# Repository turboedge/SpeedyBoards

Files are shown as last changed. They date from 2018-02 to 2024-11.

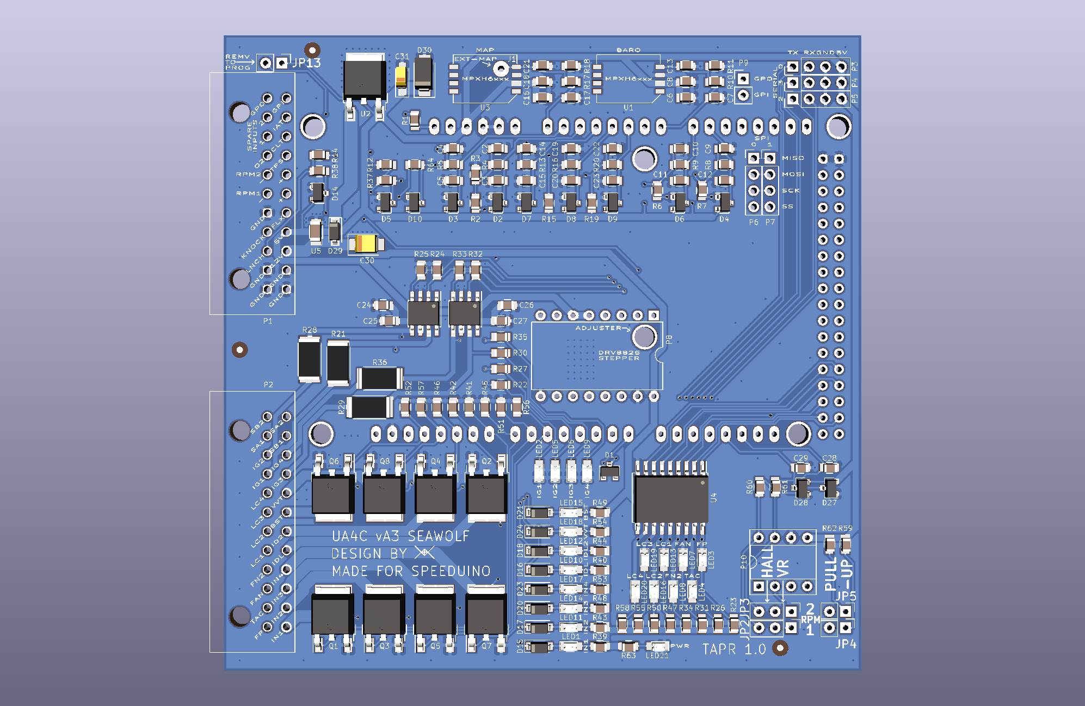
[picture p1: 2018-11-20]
UA4C/vA3-SEAWOLF/RENDER/UA4C-FRONT.png

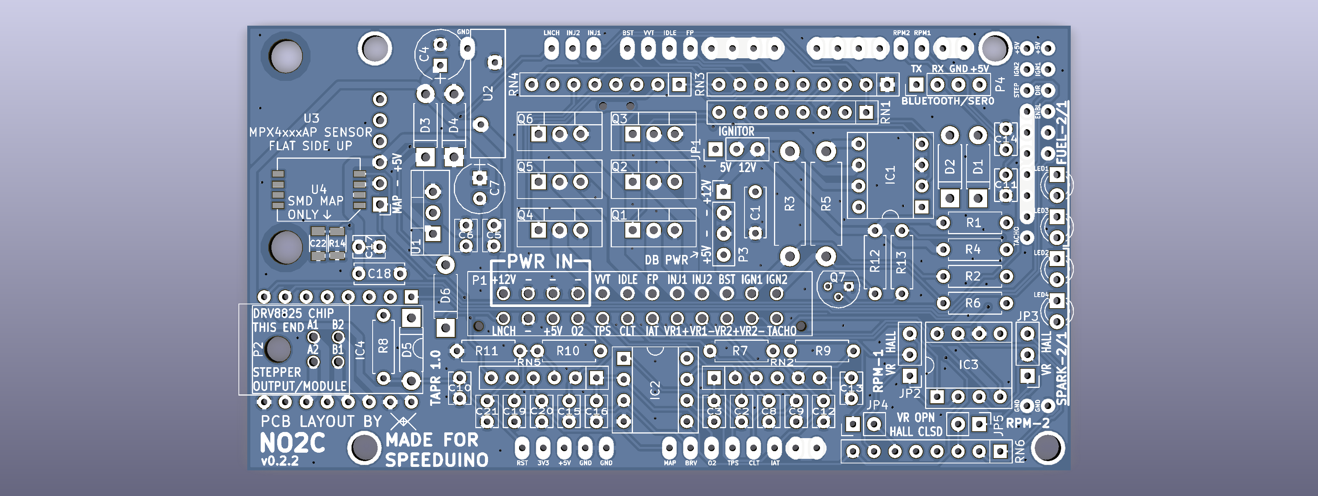
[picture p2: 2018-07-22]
NO2C/v0.2.x/v0.2.2/RENDER/NO2C-FRONT.png

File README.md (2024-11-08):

# SpeedyBoards
WTMtronics has developed several EMS PCBs designed to use the Speeduino firmware.
The Speeduino code is available here [Speeduino](https://github.com/noisymime/speeduino), but the easiest way to load the code onto your ECU is to use [SpeedyLoader](https://github.com/speeduino/SpeedyLoader).
## Ocelot
The latest ECU designed by WTMtronics builds on the UA4C that came before it, and in fact if you compare the two side by side you will see many similarities. However there have been many improvements over the previous model which are outlined in the list below.
- Automotive connector
- Reduced size
- Integrated microcontroller
- VSS input
- Flyback diodes
- Reset button

The reset button was added as the only reset connection made to the microcontroller to prevent unwanted resets from USB connected devices. There is a caveat to this arrangement though. While the first time a firmware is loaded it will go on without intervention, subsequent times will require the user to hold the reset button down then release the button when the program starts the upload process. If the upload does not start right away go back and try again.

The Ocelot uses the Silicon Labs CP2102N USB to UART controller chip. Most modern computers will detect and automatically load a driver for the COM port. If you are not getting the COM port, then you can download drivers from their website [Silicon Labs Drivers](https://www.silabs.com/developers/usb-to-uart-bridge-vcp-drivers).

Latest version: A3 *First release
### Errata
vA3:
- Labeling for trigger jumpers is reversed. The secondary trigger jumpers are nearest the outside edge of the board, and the primary trigger jumpers are near the trigger conditioner socket.
- Serial numbers prior to 002287 will not operate with out a USB connection if no Bluetooth adapter is attached. If your serial number is 002287 or higher this issue does not affect your unit. If you are affected by this issue, please contact us so we can help you [WTMtronics Help](https://wtmtronics.com/help).
## UA4C
The Under Arduino Four Channel was designed to be as small as possible wile still using a standard off the shelf Arduino MEGA and Hammond extruded enclosure. This was achieved by using SMD components and placing the Arduino upside-down on top of the PCB. The unique stacking arrangement allows the unit to be particularly thin for a unit that still uses a separate Arduino MEGA. It is a 4+4 board that incorporates the follow features.
- Four injector channels
- Four ignitor channels
- Outputs for VVT, 2x PWM idle, boost, fuel pump, tachometer, and 2x fan
- Four auxiliary outputs
- Built in stepper idle control (versions C)
- Two trigger inputs
- Launch input
- Two additional interrupt input designated as flex and knock*
- Analog inputs for CLT, IAT, TPS, and O2
- Two auxiliary analog inputs
- MAP and baro sensor onboard
- Two GPIO connections that breakout inside the case

Latest version: C6

*Knock is currently unsupported in the firmware. Either input can be used for VSS.
## NO2C
The No Overhang Two Channel was designed to incorporate as many features as possible into a through-hole board that does not exceed the dimensions of the Arduino MEGA microcontroller it sits on top of. It is a 2+2 channel board that incorporates the features below.
- Two injector channels
- Two ignitor channels
- Outputs for VVT PWM idle, boost, fuel pump, and tachometer
- Two trigger inputs
- Launch input
- Analog inputs for CLT, IAT, TPS, and O2
- MAP sensor onboard
- Socket for stepper idle control module

Latest version: D1

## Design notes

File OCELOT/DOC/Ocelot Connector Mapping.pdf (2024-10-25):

All outputs (except ignitor and stepper idle) are ground switching. Connect at least two ground terminals to a single ground source.
Connector Terminal | Arduino Pin | Function
1 | | GPI | 25 | | STEPPER IDLE A1
2 | | GPO | 26 | D34 | IGNITOR 4
3 | A8 | SPARE INPUT 1 | 27 | D33 | IGNITOR 3
4 | A9 | SPARE INPUT 2 | 28 | D28 | LOW CURRENT OUTPUT 3
5 | | 5V OUT | 29 | D27 | LOW CURRENT OUTPUT 2
6 | | KEYED 12V INPUT | 30 | D25 | FAN 2
7 | | GROUND | 31 | D22 | TACHOMETER
8 | | STEPPER IDLE A2 | 32 | D6 | INJECTOR 3
9 | | STEPPER IDLE B1 | 33 | A5 | INLET AIR TEMPERATURE SENSOR
10 | | UNSWITCHED 12V INPUT (FLYBACK FOR IDLE, BOOST, VVT) | 34 | D37 | LAUNCH/CLUTCH
11 | D29 | LOW CURRENT OUTPUT 4 | 35 | D2 | VEHICLE SPEED SENSOR
12 | D11 | VVT | 36 | D21 | KNOCK SENSOR
13 | D12 | BOOST | 37 | D18 | SECONDARY TRIGGER
14 | D10 | PWM IDLE 2 | 38 | D19 | PRIMARY TRIGGER
15 | D9 | PWM IDLE 1 | 39 | | GROUND
16 | D5 | INJECTOR 4 | 40 | | GROUND
17 | A1 | EXHAUST GAS SENSOR | 41 | | STEPPER IDLE B2
18 | A3 | THROTTLE POSITION SENSOR | 42 | D36 | IGNITOR 2
19 | A4 | COOLANT TEMPERATURE SENSOR | 43 | D35 | IGNITOR 1
20 | D20 | FLEX FUEL SENSOR | 44 | D26 | LOW CURRENT OUTPUT 1
21 | | SECONDARY TRIGGER (VR- ONLY) | 45 | D24 | FAN 1
22 | | PRIMARY TRIGGER (VR- ONLY) | 46 | D23 | FUEL PUMP
23 | | GROUND | 47 | D7 | INJECTOR 2
24 | | GROUND | 48 | D8 | INJECTOR 1
1 | 2 | 3 | 4 | 5 | 6 | 7 | 8 | 9 | 10 | 11 | 12 | 13 | 14 | 15 | 16
17 | 18 | 19 | 20 | 21 | 22 | 23 | 24 | 25 | 26 | 27 | 28 | 29 | 30 | 31 | 32
33 | 34 | 35 | 36 | 37 | 38 | 39 | 40 | 41 | 42 | 43 | 44 | 45 | 46 | 47 | 48

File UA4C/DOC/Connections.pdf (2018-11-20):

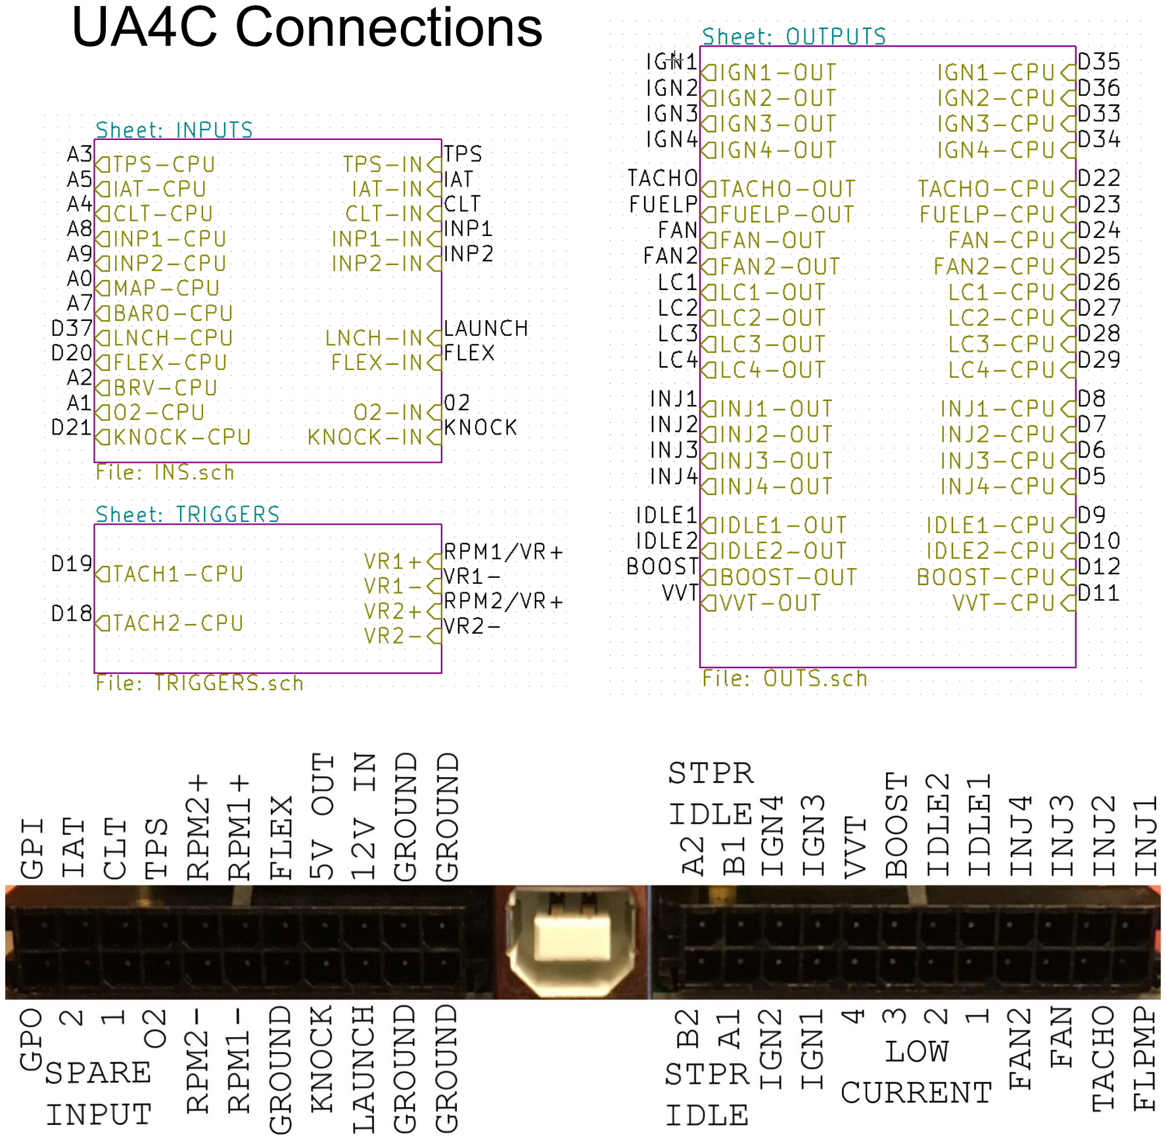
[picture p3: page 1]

UA4C Connections

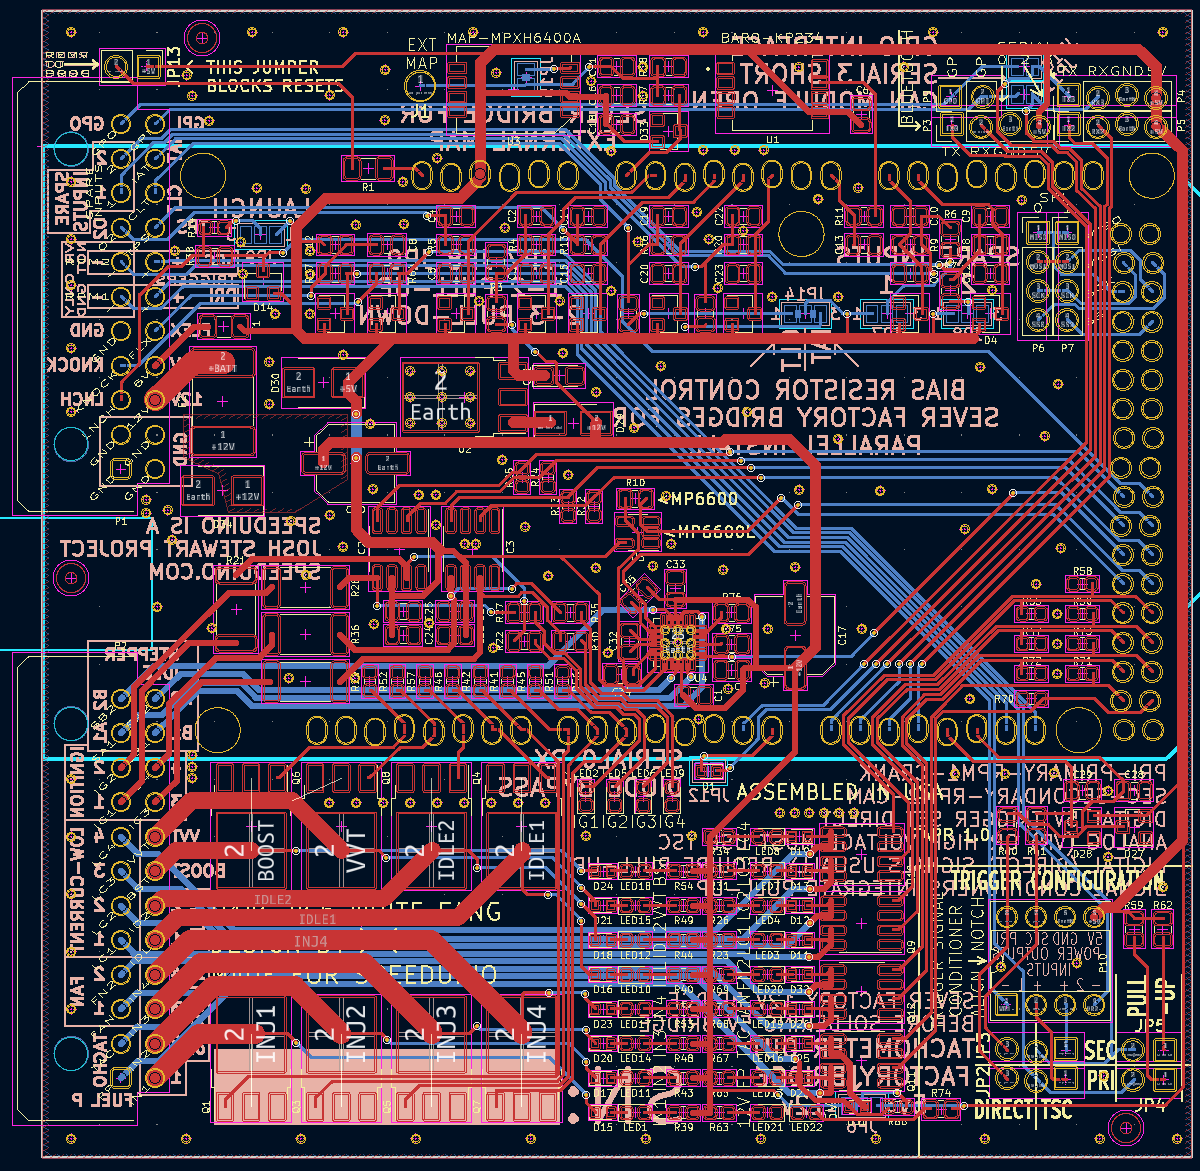
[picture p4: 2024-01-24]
UA4C/vC5-WHITE FANG/RENDER/PCB.PNG

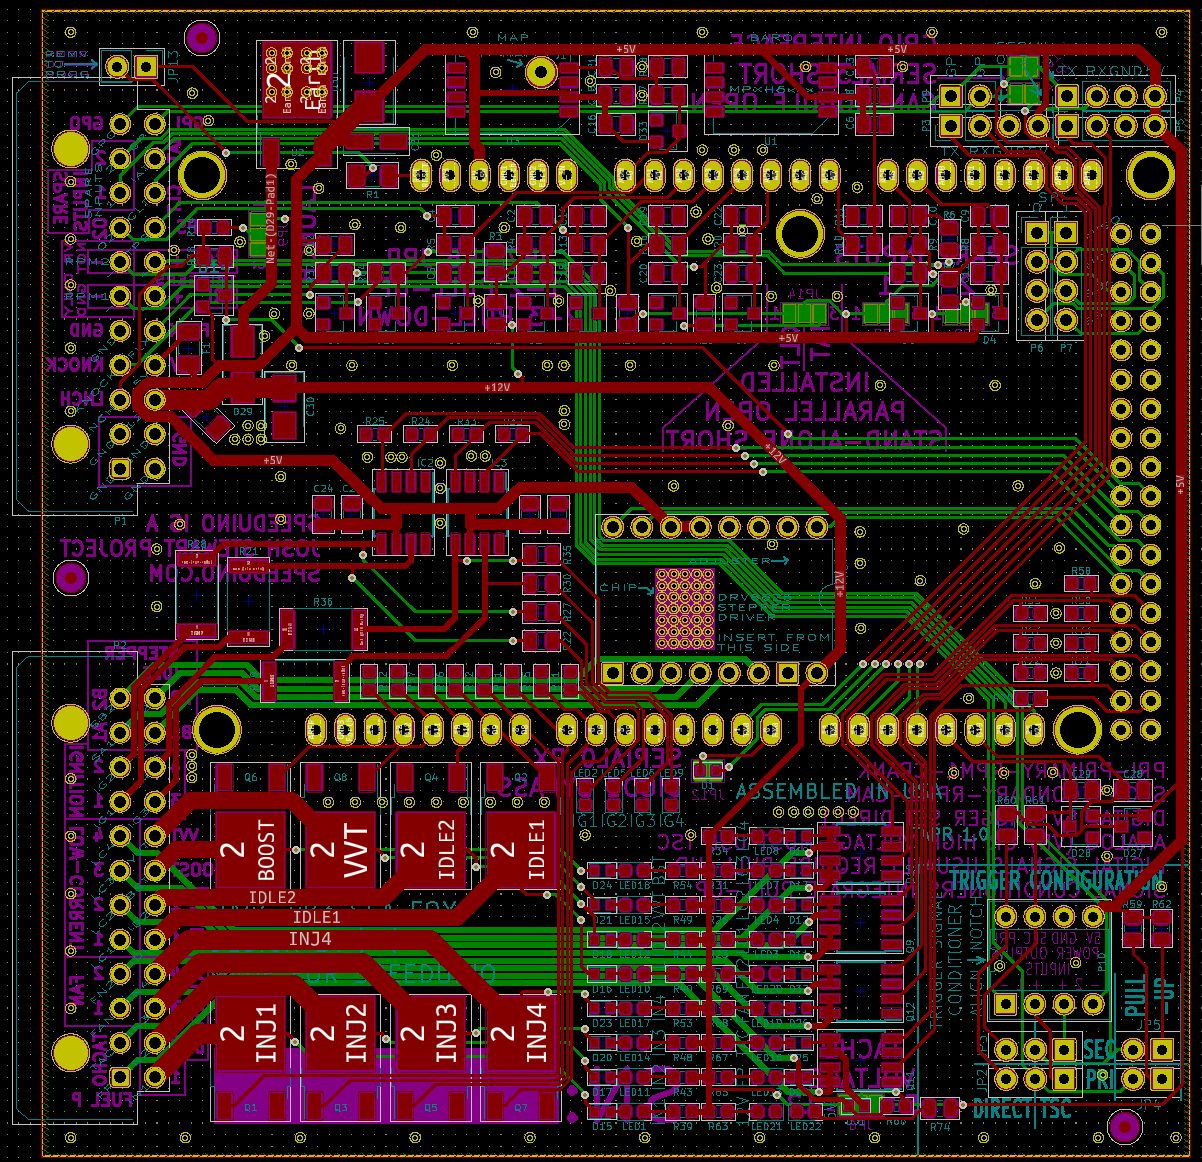
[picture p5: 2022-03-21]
UA4C/vB3-SEA FOX/RENDER/PCB.PNG

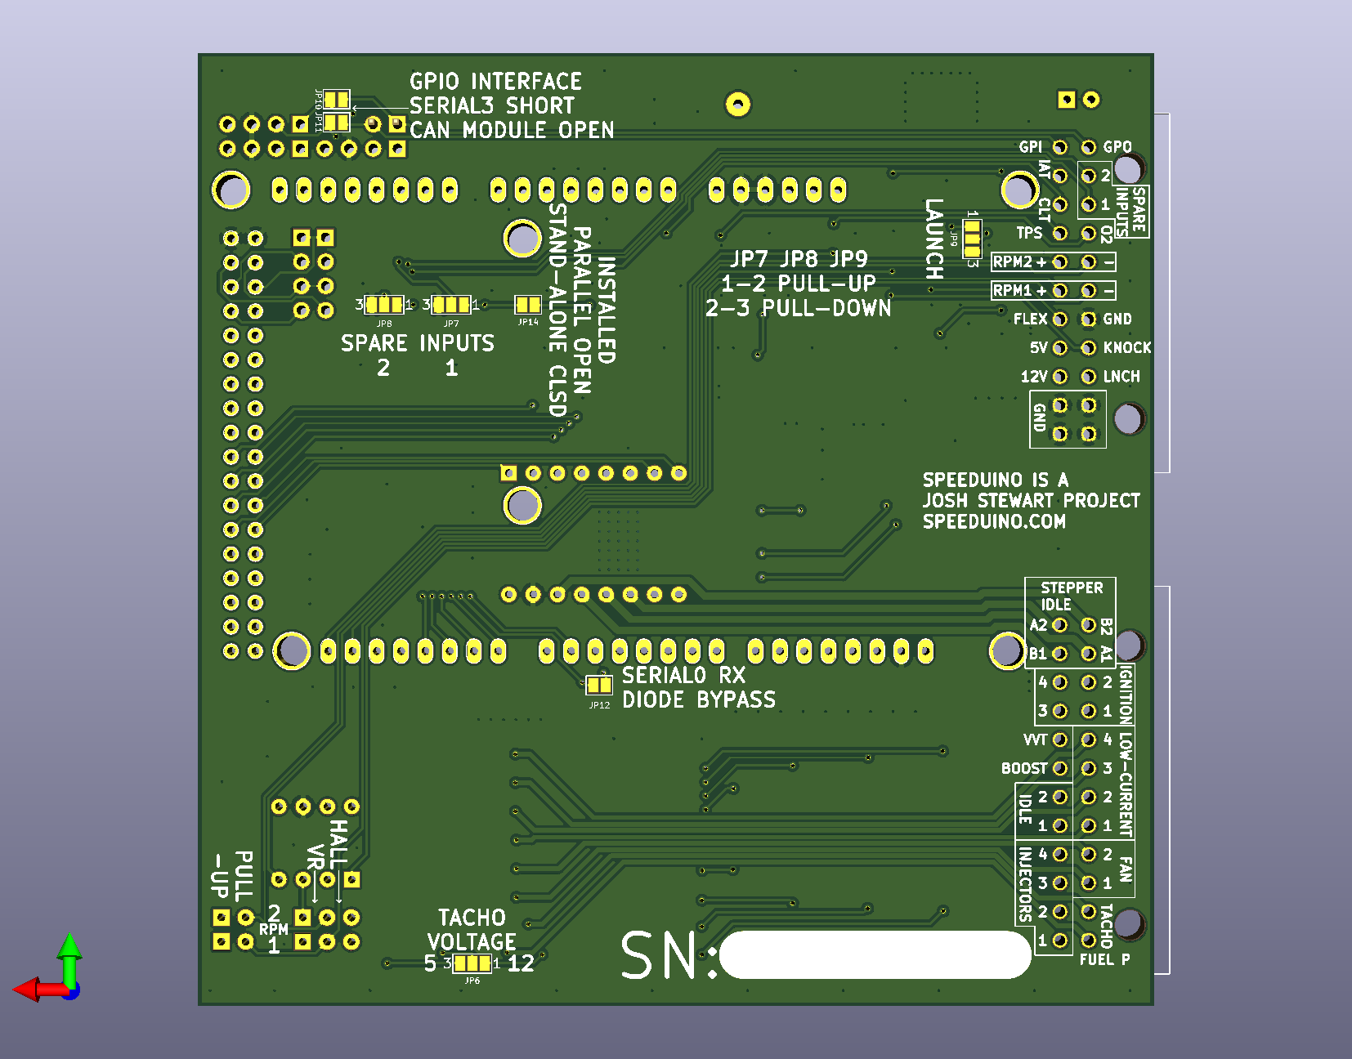
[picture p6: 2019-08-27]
UA4C/vB1-SEA FOX/RENDER/BACK.png

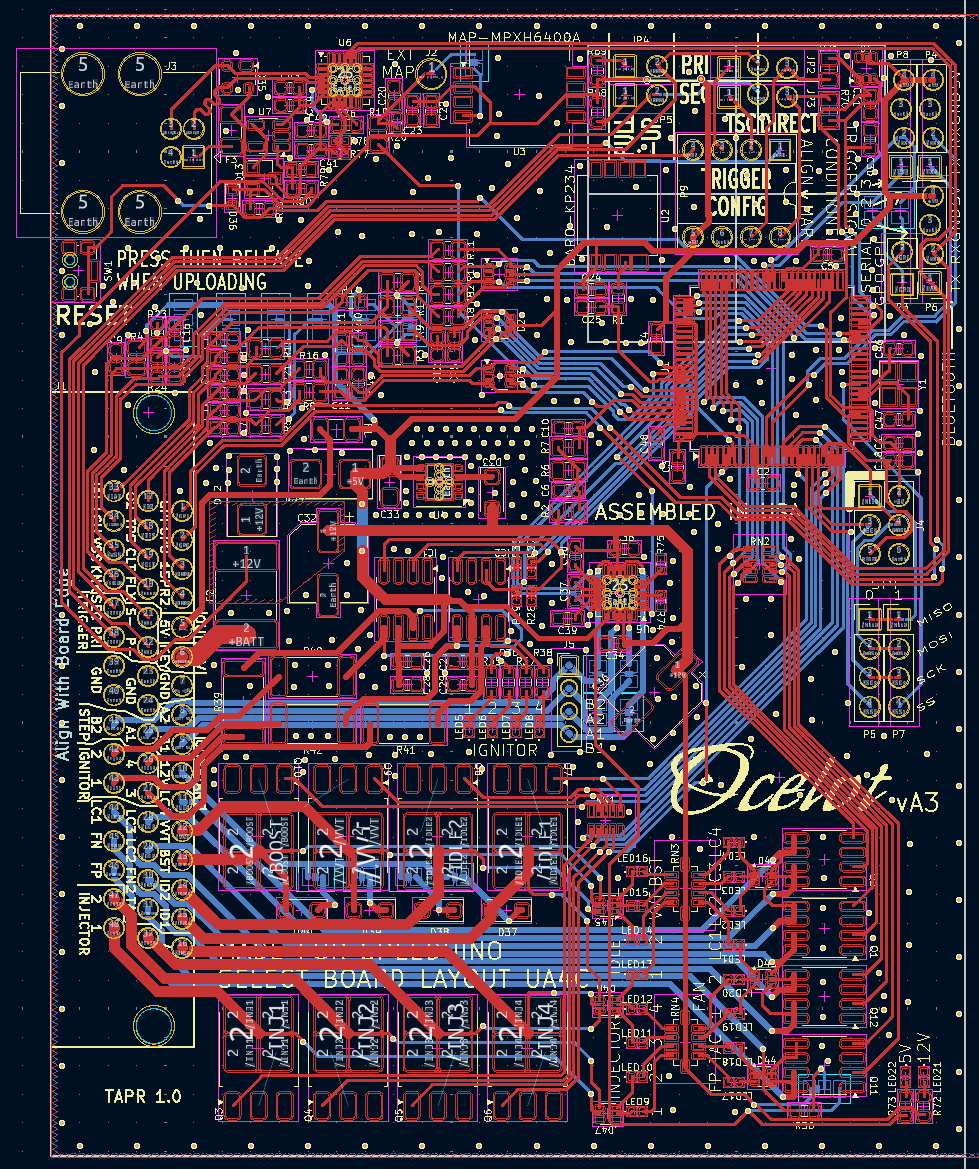
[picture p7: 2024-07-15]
OCELOT/RENDER/CAD.png

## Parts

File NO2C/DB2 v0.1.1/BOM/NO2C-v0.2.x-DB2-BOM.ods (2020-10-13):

Designator | Package | Quantity | Designation | MPN1 | MPN2 | MPN3
R13,R14 | R_1206 | 2 | 1k | RC1206JR-071KL
R1 | R_1206 | 1 | 51k | RK73H2BTTD5102F
R9,R10 | R_Axial_DIN0207_L6.3mm_D2.5mm_P7.62mm_Horizontal | 2 | 2k | MFR-25FBF52-2K
R8,R7 | R_Axial_DIN0411_L9.9mm_D3.6mm_P12.70mm_Horizontal | 2 | 47 2w | FMP200JR-52-47R
R3,R4 | R_Axial_DIN0207_L6.3mm_D2.5mm_P7.62mm_Horizontal | 2 | 1k | MFR-25FBF52-1K
R11 | R_Axial_DIN0207_L6.3mm_D2.5mm_P7.62mm_Horizontal | 1 | 470r | MFR-25FBF52-470R
R6,R5 | R_Axial_DIN0207_L6.3mm_D2.5mm_P7.62mm_Horizontal | 2 | 100k | MFR-25FBF52-100K
R12,R2 | R_Axial_DIN0207_L6.3mm_D2.5mm_P7.62mm_Horizontal | 2 | 2k49 0.1% | YR1B2K49CC
RN1 | R_Array_SIP6 | 1 | 470r | 4606X-102-471LF | L063S471LF
D4,D6,D5,D3 | SOT-23 | 4 | BAT54S | BAT54SRF
D1,D2 | LED_D3.0mm | 2 | T1 RED | SLX-LX3044HD | LTL-4221N
C3 | C_1206 | 1 | 47p | CL31C470JCCNNNC
C5 | C_Disc_D3.8mm_W2.6mm_P2.50mm | 1 | u1 | K104K15X7RF53L2 | RCER71H104K0DBH03A
C1 | C_Disc_D3.8mm_W2.6mm_P2.50mm | 1 | u01 | SR155C103KARTR1 | K103K15X7RF5TL2
C6 | C_Disc_D3.8mm_W2.6mm_P2.50mm | 1 | u22 | FK18X7R1H224K | FG18X7R1H224KRT06 | RHEL81H224K1A2H03B
C4,C2 | C_Disc_D6.0mm_W2.5mm_P5.00mm | 2 | 1u | RDER71H105K2K1H03B
IC2 | DIP-8_W7.62mm | 1 | ICL7667 | IXDN602PI | TC4424AVPA | TC4424EPA
IC1 | SOIC-16_3.9x9.9mm_Pitch1.27mm | 1 | ULN2003A | ULN2003AIDR
U1 | NXP_Pressure_Sensor_SSOP | 1 | DIL8 | MPXHZ6115A6U
P1 | Board Mount 3mm connector-12 position |  |  | 4-794630-2
P2 | Included in 4 position header socket count
P3 | Pigtail for Bluetooth
 | Long tail header pins for NO2C 18 pins required | 1 |  | 929834-03-18 | 929834-03-36 | RK versions ok, p#s are half and full strip
 | 2 position header socket | 3 |  | 75915-302LF
 | 4 position header socket | 2 |  | 75915-304LF
 | 6 position header socket | 1 |  | 75915-306LF
 | Wire Housing 3mm connector-12 position |  |  | 1-794617-2 | From car harness
 | Female pins for above |  |  | 794606-1
 | Panel Mount 3mm housing-12 position |  |  | 1-794615-2 | If you want to route all connections to end of case
 | Male pins for above |  |  | 1-794608-0

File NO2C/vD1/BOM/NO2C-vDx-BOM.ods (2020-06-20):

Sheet: Sheet1
Designator | Package – Description | Quantity | Designation | MPN1 | MPN2 | MPN3 | Alt Value
D3,D5,D6 | D_DO-41_SOD81_P7.62mm_Horizontal – Diode, Schottky | 3 | 1N5818 | 1N5818 | 1N5819
D4 | D_DO-41_SOD81_P7.62mm_Horizontal – Diode, Zener, 5.6v | 1 | 1N5919BG | 1N5919BG | 1N4734A
D2,D1 | D_DO-41_SOD81_P7.62mm_Horizontal – Diode | 2 | 1N4004 | 1N4004
R8 | R_Axial_DIN0207_L6.3mm_D2.5mm_P7.62mm_Horizontal | 1 | 56r | MFR-25FBF52-56R
R12 | R_Axial_DIN0207_L6.3mm_D2.5mm_P7.62mm_Horizontal | 1 | 10k | MFR-25FBF52-10K
R1,R2,R4,R6 | R_Axial_DIN0207_L6.3mm_D2.5mm_P7.62mm_Horizontal | 4 | 2k | MFR-25FBF52-2K
R13,R15 | R_Axial_DIN0207_L6.3mm_D2.5mm_P7.62mm_Horizontal | 2 | 1k | MFR-25FBF52-1K
R3,R5 | R_Axial_DIN0411_L9.9mm_D3.6mm_P12.70mm_Horizontal | 2 | 47r 2w | FMP200FRF52-160R | ERG-2SJ161 | PR02000201600JR500 | (16r 2w for 5v only) RR02J16RTB
R11 | R_Axial_DIN0207_L6.3mm_D2.5mm_P7.62mm_Horizontal | 1 | 1k 0.1% | YR1B1K0CC | MFP-25BRD52-1K
R10 | R_Axial_DIN0207_L6.3mm_D2.5mm_P7.62mm_Horizontal | 1 | 3k9 0.1% | MFP-25BRD52-3K9 | YR1B3K92CC
R9,R7 | R_Axial_DIN0207_L6.3mm_D2.5mm_P7.62mm_Horizontal | 2 | 2k49 0.1% | YR1B2K49CC
RN4,RN1,RN6 | R_Array_SIP8 | 3 | 1k | 4608X-102-102LF | CSC08A031K00GEK
RN5,RN2 | R_Array_SIP6 | 2 | 470r | 4606X-102-471LF | L063S471LF
RN3 | R_Array_SIP9_Bussed | 1 | 100k | 4609X-101-104LF | CSC09A01100KGEK
LED4,LED2,LED3,LED1 | LED_D3.0mm | 4 | T1 <=10mcd | SLX-LX3044HD | LTL-4221N
C11,C17 | Capacitor_Ceramic_Disc_D3.8mm_W2.6mm_P2.50mm | 2 | u01 50v X7R | SR155C103KARTR1 | K103K15X7RF5TL2
C14,C16,C20,C13,C9,C3 | Capacitor_Ceramic_Disc_D3.8mm_W2.6mm_P2.50mm | 6 | u22 50v X7R | FK18X7R1H224K | FG18X7R1H224KRT06 | RHEL81H224K1A2H03B
C18,C1 | Capacitor_Ceramic_Disc_D6.0mm_W2.5mm_P5.00mm | 2 | 1u 50v X7R | RDER71H105K2K1H03B
C21 | Capacitor_Ceramic_Disc_D3.8mm_W2.6mm_P2.50mm | 1 | u33 50v X7R | RCER71H334K1A2H03B | FG18X7R1H334KRT06 | RHEL81H334K1A2H03B
C5,C15,C19,C2,C12,C8,C6 | Capacitor_Ceramic_Disc_D3.8mm_W2.6mm_P2.50mm | 7 | u1 50v X7R | K104K15X7RF53L2 | RCER71H104K0DBH03A
C4 | Capacitor_Radial_Tantalum_D6.0mm_P2.50mm | 1 | 10u 35v | TAP106K035SCS | T350G106K035AT
C7 | Capacitor_Radial_Tantalum_D6.0mm_P2.50mm | 1 | 47u 6.3v | TAP476K006SCS | T350F476K006AT
U1 | TO-220_Vertical – 5V 1A LDO | 1 | LM2940T-5.0 | LM2940T-5.0/NOPB | LM2940T-5.0/LF08 | L4941BV
U2 | Varistor_Disc_D15.5_W4.2_P7.5 | 1 | ERZ | ERZ-V14D220 | B72214S0140K101
IC4 | 8 POSITION 2.54MM FEMALE SOCKET | 2 | DRV8825 | 75915-308LF | 929974-01-08-RK
IC3 | 4 POSITION 2.54MM FEMALE SOCKET | 2 | Dual VR | 75915-304LF | 929974-01-04-RK
IC2 | DIP-8_W7.62mm | 1 | SP721 | SP721APP
IC1 | DIP-8_W7.62mm | 1 | TC4424 | IXDN602PI | TC4424AVPA | TC4424EPA
Q4,Q3,Q6,Q5,Q2,Q1 | TO-220_Vertical | 6 | STP62NS04Z | STP62NS04Z | STP75NS04Z
Q7 | TO-92 | 1 | 2N6517 | 2N6517BU | PN2222
P1 | Molex_Microfit3_Header_02x12_Straight_43045-2428 | 1 |  | 43045-2412 | 5-794630-4
P2 | Molex_Microfit3_Header_02x02_Angled_43045-040x | 1 |  | 43045-0400
P3 | Pin_Header_Straight_1x04_Pitch2.54mm | 1
JP5,JP4 | Pin_Header_Straight_1x02_Pitch2.54mm | 2
JP3,JP2,JP1 | Pin_Header_Straight_1x03_Pitch2.54mm | 3
U3 | MPX4250A | 1 | MPX4250A | MPX4250AP | MPX4400AP (400 kPa version)
 | SHUNT | 5 |  | 2-382811-1 | STC02SYAN
 | 1 POSITION 2.54MM MALE TIN | 60 |  | 68001-400HLF | (8 position) PREC008SAAN-RC
 | DIP-8_W7.62mm_Socket NOT RECOMMENDED FOR IC2 | 1 |  | 110-99-308-41-001000 | AR 08 HZL-TT
From car harness | Wire Housing 3mm connector-24 position |  |  | 2-794617-4
From car harness for stepper | Wire Housing 3mm connector-4 position |  |  | 794617-4
 | Female pins for above |  |  | 794606-1
For routing 24-pins to case end | Panel Mount 3mm housing-24 position |  |  | 2-794615-4
 | Male pins for above |  |  | 1-794608-0

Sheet: Sheet2
1N5818 | 2
1N5919BG | 1
1N4004 | 2
MFS1/4DCT52R1002F | 2
SFR16S0006800JA500 | 4
PR02000201600JR500 | 2
MFP-25BRD52-3K9 | 1
MFS1/4DCT52R2491F | 2
MFS1/4DCT52R1001F | 2
4608X-102-102LF | 3
4606X-102-471LF | 2
4609X-101-104LF | 1
SLX-LX3044HD | 4
SR155C103KARTR1 | 2
FK18X7R1H224K | 6
K472K15X7RF5TL2 | 1
FK14X7R1H105K | 2
RCER71H334K1A2H03B | 1
K104K15X7RF53L2 | 7
TAP106K035SCS | 1
TAP476K006SCS | 1
LM2940T-5.0/NOPB | 1
ERZ-V14D220 | 1
929974-01-08-RK | 2
929974-01-04-RK | 2
SP721APP | 1
IXDN602PI | 1
STP62NS04Z | 6
PN2222 | 1
1-640456-2 | 1
1-640456-6 | 1
640456-4 | 1
MPX4250AP | 1
2-382811-1 | 5
68000-408HLF | 8
3-640620-2 | 3
3-640620-3 | 2
3-640620-4 | 5
110-99-308-41-001000 | 2

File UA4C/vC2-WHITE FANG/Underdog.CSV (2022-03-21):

Reference | Quantity | Value | Footprint | Datasheet | MPN | PN
C1 C2 C4 C6 C9 C10 C14 C16 C19 C22 C25 C27 C29 C32 C33 | 15 | u1 | Capacitor_SMD:C_0805_2012Metric |  | CL21B104KBFNNNE
C3 C5 C11 C12 C15 C20 C23 C34 | 8 | u22 | Capacitor_SMD:C_0805_2012Metric |  | CL21B224KBFNNNE
C7 C8 C18 C24 C26 C35 | 6 | 1u | Capacitor_SMD:C_0805_2012Metric |  | CL21B105KBFNNNE
C13 C21 | 2 | 47p | Capacitor_SMD:C_0805_2012Metric |  | CL21C470JBANNNC
C28 | 1 | u01 | Capacitor_SMD:C_0805_2012Metric |  | CL21B103KBCNNNC
C17 C30 | 2 | 47u 50v | Capacitor_SMD:CP_Elec_6.3x5.4 | https://datasheet.octopart.com/EEE-FT1H470AL-Panasonic-datasheet-147569663.pdf | EEE-FT1H470AL
C31 | 1 | 47u | Capacitor_Tantalum_SMD:CP_EIA-3216-18_Kemet-A |  | T55A476M6R3C0200 | TCJK476M006R0200
D1 D11 D12 D13 D15 D16 D17 D18 D19 D20 D21 D22 D23 D24 D25 D26 D31 D32 | 18 | BAS70KFILM | Diode_SMD:D_SOD-523 |  | BAS70-02V-V-G-08
D29 | 1 | 60V 1A | Diode_SMD:D_SMA | https://www.diodes.com/assets/Datasheets/ds13002.pdf | B160-E3/61T
D30 | 1 | 1SMB5919BT3G | Diode_SMD:D_SMB | https://www.mouser.com/datasheet/2/308/1SMB5913BT3-D-1292981.pdf | 1SMB5919BT3G | 1SMB5919BT3G
D2 D3 D4 D5 D6 D7 D8 D9 D10 D14 D27 D28 D33 | 13 | BAT54S | Package_TO_SOT_SMD:SOT-23 |  | BAT54S,215
F1 | 1 | 500mA/1A 24V | Fuse:Fuse_1206_3216Metric | https://www.mouser.com/datasheet/2/643/ds-CP-0zcj-series-1664160.pdf | 0ZCJ0050AF2E
IC2 IC3 | 2 | IXDN602SIA | Package_SO:SOIC-8_3.9x4.9mm_P1.27mm |  | IXDN602SIA
J1 | 1 | External MAP Conn | Wire_Pads:SolderWirePad_single_1mmDrill | ~ | DNP
JP10 JP11 JP12 | 3 | SolderJumper_2_Open | Jumper:SolderJumper-2_P1.3mm_Open_Pad1.0x1.5mm |  | DNP
JP4 JP5 JP13 | 3 | PULLUP | footprnt:JPR_2POS_SMLHL |  | DNP
JP14 | 1 | SO/PARA | Connector_Automotive:SolderJumper-3_P1.3mm_Bridged123_Pad1.0x1.5mm_NumberLabels |  | DNP
JP15 | 1 | Onboard MAP Enable | Jumper:SolderJumper-2_P1.3mm_Bridged_Pad1.0x1.5mm | ~ | DNP
JP2 JP3 | 2 | HALL_VR | footprnt:JPR_3POS_SMLHL |  | DNP
JP6 | 1 | TACHSEL | Jumper:SolderJumper-3_P1.3mm_Bridged12_Pad1.0x1.5mm_NumberLabels |  | DNP
JP7 JP8 JP9 | 3 | PULLUPDWN | Jumper:SolderJumper-3_P1.3mm_Open_Pad1.0x1.5mm_NumberLabels |  | DNP
LED1 LED2 LED3 LED4 LED5 LED6 LED7 LED8 LED9 LED10 LED11 LED12 LED13 LED14 LED15 LED16 LED17 LED18 LED19 LED20 LED21 LED22 | 22 | RED | LED_SMD:LED_0603_1608Metric |  | SML-310LTT86
P1 | 1 | INPUTS | Connector_Molex:Molex_Micro-Fit_3.0_43045-2200_2x11_P3.00mm_Horizontal |  | DNP
P10 | 1 | Dual VR C | Housings_DIP:DIP-8_W7.62mm_Socket |  | DNP
P2 | 1 | OUTPUTS | Connector_Molex:Molex_Micro-Fit_3.0_43045-2400_2x12_P3.00mm_Horizontal |  | DNP
P3 | 1 | SER0 | Pin_Headers:Pin_Header_Straight_1x04_Pitch2.54mm |  | DNP
P4 | 1 | SER3 | Pin_Headers:Pin_Header_Straight_1x04_Pitch2.54mm |  | DNP
P5 | 1 | SER2 | Pin_Headers:Pin_Header_Straight_1x04_Pitch2.54mm |  | DNP
P6 | 1 | SPI0 | Pin_Headers:Pin_Header_Straight_1x04_Pitch2.54mm |  | DNP
P7 | 1 | SPI1 | Pin_Headers:Pin_Header_Straight_1x04_Pitch2.54mm |  | DNP
P9 | 1 | CAN | Connector_PinHeader_2.54mm:PinHeader_1x02_P2.54mm_Vertical |  | DNP
Q1 Q2 Q3 Q4 Q5 Q6 Q7 Q8 | 8 | NCV8406 | Package_TO_SOT_SMD:TO-252-2 |  | NCV8406BDTRKG
Q9 Q10 Q11 Q12 | 4 | NCV8402AD | Package_SO:SOIC-8_3.9x4.9mm_P1.27mm | www.st.com/resource/en/datasheet/CD00001537.pdf | NCV8402ADDR2G
R1 | 1 | 56r | Resistor_SMD:R_1206_3216Metric |  | RK73H2BTTD56R0F
R14 R23 R26 R31 R34 R39 R40 R43 R44 R48 R49 R53 R54 R63 R65 R66 R67 R68 R69 | 19 | 2k7 | Resistor_SMD:R_0603_1608Metric |  | RK73B1JTTD272J
R6 R7 R12 R15 R19 | 5 | 2k49 0.1% | Resistor_SMD:R_0805_2012Metric |  | ERA6AEB2491V
R11 R18 R75 | 3 | 51k | Resistor_SMD:R_0805_2012Metric |  | RK73H2ATTD5102F
R2 | 1 | 3k9 0.1% | Resistor_SMD:R_0805_2012Metric |  | ERA6AEB392V
R4 R5 R8 R9 R10 R13 R16 R17 R20 R22 R27 R30 R35 R37 R38 R64 R74 | 17 | 470r | Resistor_SMD:R_0805_2012Metric |  | RK73H2ATTD4700F
R24 R25 R32 R33 R41 R42 R45 R46 R47 R50 R51 R52 R55 R56 R57 R58 R70 R71 R72 R73 | 20 | 100k | Resistor_SMD:R_0603_1608Metric |  | RK73B1JTTD104J
R3 | 1 | 1k 0.1% | Resistor_SMD:R_0805_2012Metric |  | ERA6AEB102V
R21 R28 R29 R36 | 4 | 15r | Resistor_SMD:R_2512_6332Metric |  | RK73H3ATTE15R0F
R60 R61 | 2 | 220r | Resistor_SMD:R_0805_2012Metric |  | RK73H2ATTD2200F
R59 R62 | 2 | 1K | Resistor_SMD:R_0805_2012Metric |  | RK73H2ATTD1001F
R76 | 1 | 220k | Resistor_SMD:R_0805_2012Metric |  | RK73H2ATTD2203F
SHIELD1 | 1 | ARDUINO_MEGA_SHIELD | footprnt:ARDUINO_MEGA_SHIELD |  | DNP
U1 | 1 | BARO | Sensors:NXP_Pressure_Sensor_SSOP |  | MPXH6115A6T1
U2 | 1 | TS2940CP50 | Package_TO_SOT_SMD:TO-252-2 |  | TS2940CP50 ROG
U3 | 1 | MAP | Sensors:NXP_Pressure_Sensor_SSOP |  | MPXH6400AC6U
U4 | 1 | MP6600 | Package_DFN_QFN:QFN-24-1EP_4x4mm_P0.5mm_EP2.7x2.7mm_ThermalVias | https://www.monolithicpower.com/en/documentview/productdocument/index/version/2/document_type/Datasheet/lang/en/sku/MP6600/ | MP6600GR-Z
U5 | 1 | 14v | Capacitor_SMD:C_1206_3216Metric |  | ZV14K1206201NIR1HT

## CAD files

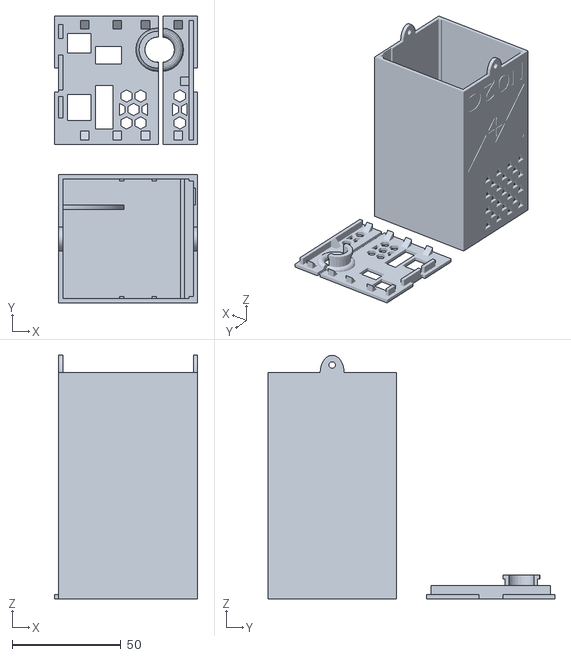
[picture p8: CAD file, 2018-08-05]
Set-NOboxT.stl
66.0 x 132.0 x 112.0

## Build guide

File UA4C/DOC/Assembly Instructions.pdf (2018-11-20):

# UA4C Assembly Instructions

## Use the following directions to turn your mostly assembled UA4C into a

fully assembled UA4C.

If you are going install a stepper driver the best time is now. Insert the module through top of the board with the adjustment pot over the hole in the hole in the UA4C. Flip the UA4C over and solder the pins down and clip the remaining off.

The next step is to attach the BARO and MAP sensors. Pay attention to the clipped corner of the sensor and align it with the markings on the on the board. vA3 has solder already on the sensor pads. Use this solder to tack one of the sensor legs and then adjust its position if necessary. If you have access to flux this can help get it to stick. Now use the finest solder wire available and solder the rest of the legs and touch up the first one if necessary.

Now attach the Arduino and trigger jumper header pins to the top of the board. You should have three strips of 40 pins. Break one of the sticks into five sections of eight and insert them into the board. Take another strip and break four pins off and then break both the section of four and the section of 36 in half. Insert the two pin pieces in the jumper positions where the VR socket will go and the 18 pin pieces in the double row Arduino connection. You will now be left with one more stick. Break one ten and two six pin sections off. Put the ten and one of the six pin sections into the appropriate Arduino locations. The remaining six pin section gets broken in half and used in the final jumper positions by the VR socket. Now take a ~10cm² piece of something flat but not easily melted (a piece of good cardboard) and set it on top of the board. Avoid the MAP sensor as it protrudes. Now flip the sandwich you have created over, again be careful of the MAP sensor, you may need to let it hang off the edge of a table. Press down a bit to make sure all the pins are fully through the board and solder away.

The next step is to attach the VR module socket. Break off two four pin strips from your remaining header pins. Insert them into the sockets suchasthat they create a square. Insert the sockets into the board and while holding them in flip the board and carefully tack a pin in each row with solder. Set the board down and solder the remaining socket pins. Remove the header pins from the socket.

Final step is the card edge with the harness connectors and reset protection jumper. The header jumper can simply be pressed in to its spot in the corner and soldered down. For the harness connectors snap both of them to the board. Now on each connector solder ONE of the middle pins toward the outside edge. Now while squeezing the connector and the PCB together with your finger in the middle of the connector and over ther outside row heat the solder. The connector will snap tight to the board and become level. Repeat for the other connector and then solder all the contacts.

Congrats! You’re Done!

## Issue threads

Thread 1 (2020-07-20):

Some parts missing in BOM vD1

romP44, 2020-07-20:
Hello,
In BOM vD1, some parts are missing:
- P4
- JP6
- C22
- R14

turboedge, 2022-03-22:
I checked over the BOM, and the parts you are referring to are header pins and jumpers. That said some of the parts are a bit out of date with what I currently ship with the kits I send out. I'll try to get this updated soon. I will not be updating the BOMs for the old versions though.

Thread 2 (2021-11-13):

Board is at VC3, source is at VB2?

ElDominio, 2021-11-13:
I saw that there's aa VC3 for sale, but the source only goes to an old revision. Can the source be updated? It is a very good reference for electronic design.

rickyrockrat, 2022-03-20:
I bought a UA4C but no source, so I have no idea what I really have. I wish I had realized this before I bought it. I would have found something else.

turboedge, 2022-03-21:
The files are now posted, sorry for the delay.

rickyrockrat, 2022-03-23:
Thanks! I just built the speeduino from source using this project:
https://github.com/rickyrockrat/speeduino-build

Are there any files I should know about as far as pin mapping? I will work through the schematic and verify the pins are right, but didn't know if you need to supply a header file.  Thanks for the board, BTW! I hope to have my 1uzfe running here soon.

turboedge, 2022-03-23:
Sorry you lost me. Verify what pins, header file? I hope your project goes smoothly.

Closed 2022-03-21.

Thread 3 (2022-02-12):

UA4C BOM?

digitaltrousers, 2022-02-12:
Hi. I notice there are folders with a BOM inside the folders for NO2C. Sorry if I've missed something, but is there a BOM for UA4C?
Thanks.

turboedge, 2022-03-21:
If you open the project source code in Kicad the items are listed there. Good luck finding all the parts, it's been a nightmare.

Closed 2022-03-21.

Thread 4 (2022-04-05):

Updated Assembly Instructions for UA4C vC3 White Fang

masterofsome906, 2022-04-05:
Weaver, Looking to collaborate on updating the assembly instructions for the current UA4C White Fang board.  I've based my writeup on your original and have geared it towards individuals looking to get into the platform without much/any experience with the earlier versions.

masterofsome906, 2022-04-05:
[UA4C vC3 White Fang Assembly Instructions.pdf](https://github.com/turboedge/SpeedyBoards/files/8413895/UA4C.vC3.White.Fang.Assembly.Instructions.pdf)

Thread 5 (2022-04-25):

BAT54S Diode pinout not as shown in schematics?

Afroboltski, 2022-04-25:
The BAT54S datasheet ([https://assets.nexperia.com/documents/data-sheet/BAT54_SER.pdf](https://assets.nexperia.com/documents/data-sheet/BAT54_SER.pdf)) shows the following pinout:

Pin1: Anode
Pin2: N/C
Pin3: Cathode

However in the schematics, e.g. [https://github.com/turboedge/SpeedyBoards/blob/master/UA4C/vB3-SEA%20FOX/SCHEM/Underdog.pdf](https://github.com/turboedge/SpeedyBoards/blob/master/UA4C/vB3-SEA%20FOX/SCHEM/Underdog.pdf), the diodes (e.g. page 2, diode D7) are shown as doubled up, e.g. as if the pinout was as follows:

Pin1: Anode diode 1
Pin2: Cathode Diode 2
Pin3: Cathode Diode 1/Anode diode 2

Using the pinout from the datasheet, you would only have a diode from GND to INPUT, not from INPUT to +5V as shown.

Or is there a different version of the BAT54S that I'm not seeing?

Afroboltski, 2022-04-25:
Never mind me, I mixed up my BAT54 and BAT54S...

Closed 2022-04-25.

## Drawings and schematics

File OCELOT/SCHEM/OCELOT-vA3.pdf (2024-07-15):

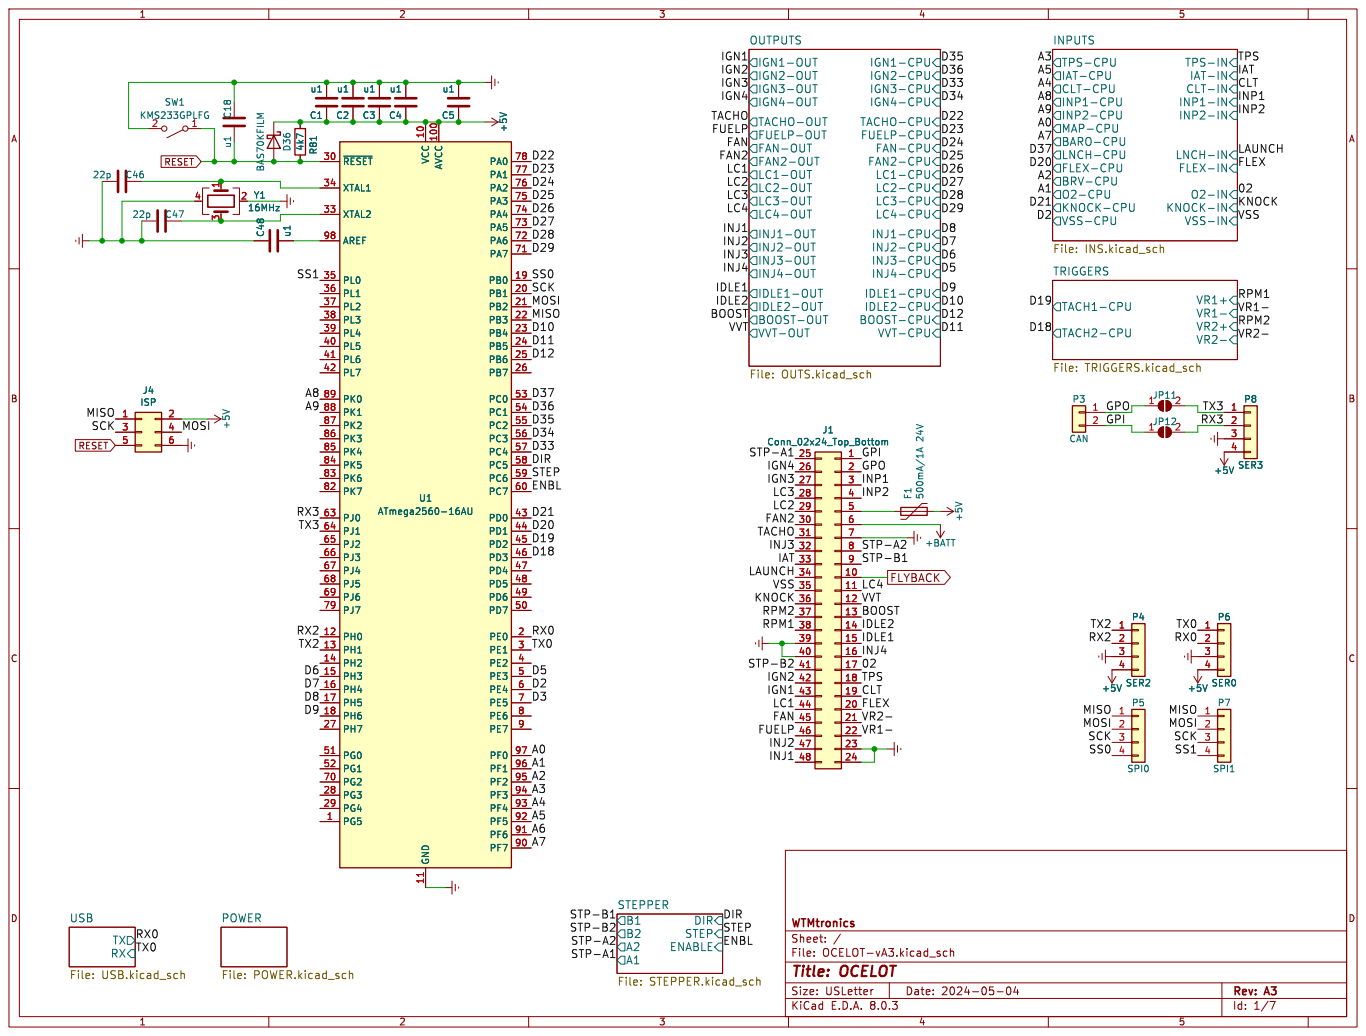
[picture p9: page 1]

File: OCELOT-vA3.kicad_sch Sheet: / WTMtronics TXRX USB

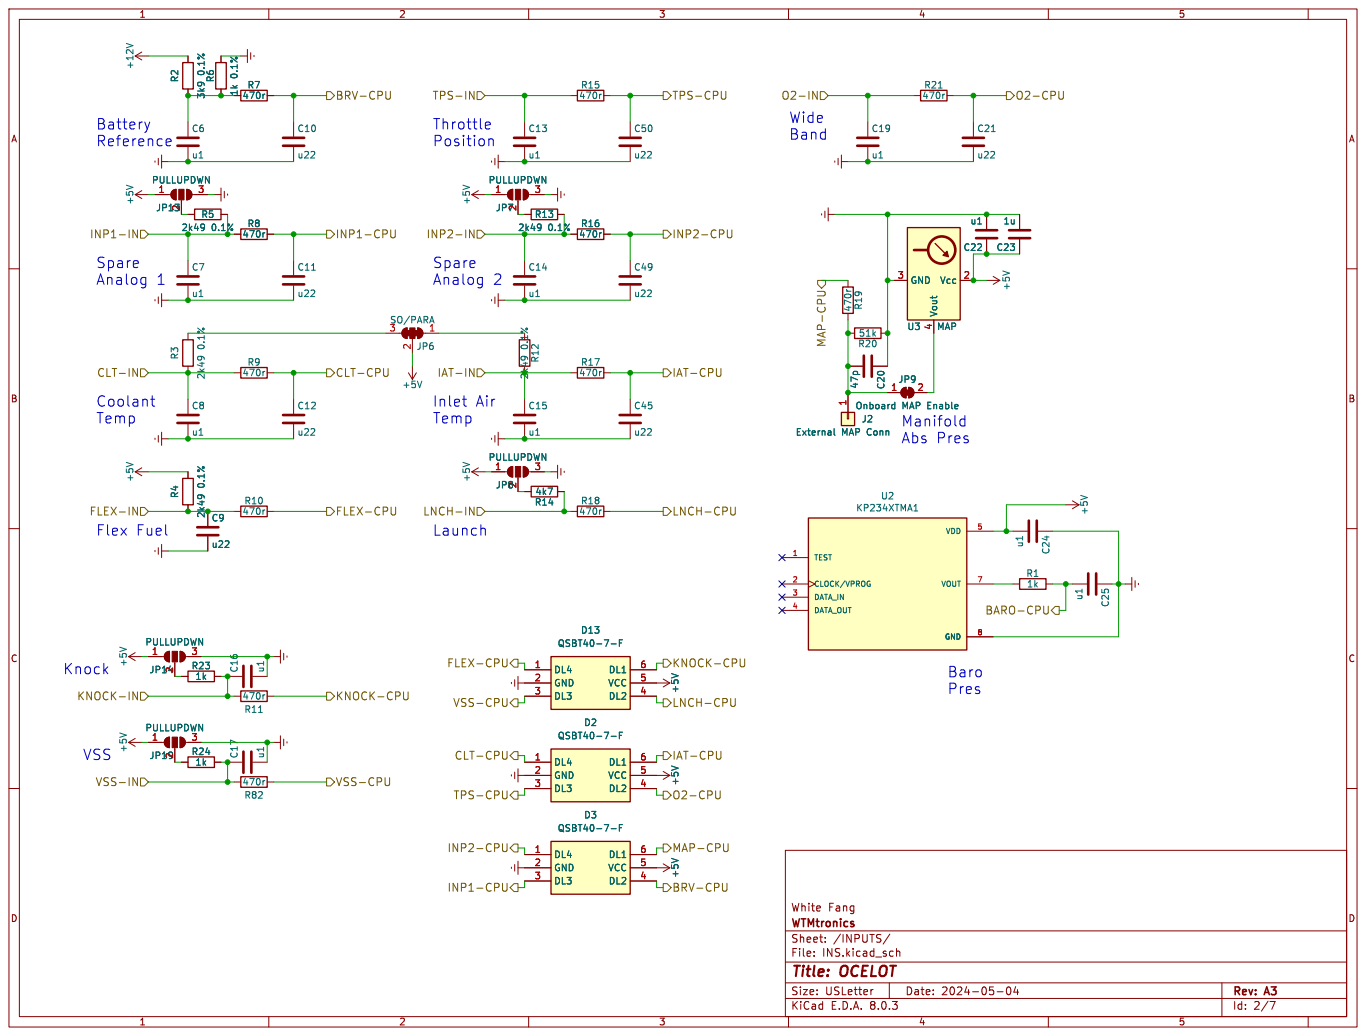
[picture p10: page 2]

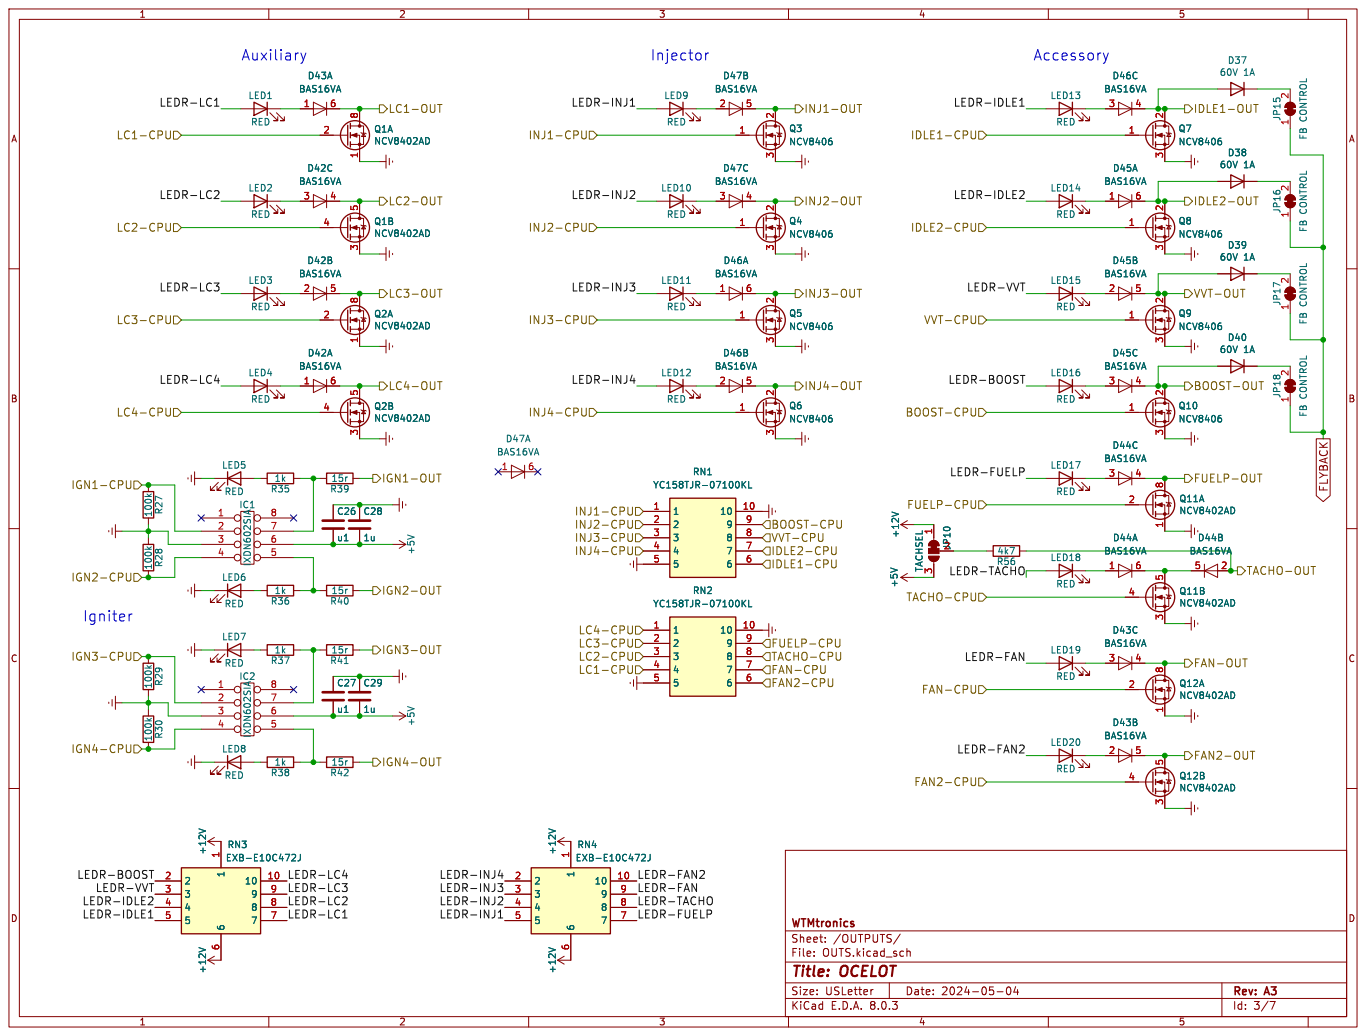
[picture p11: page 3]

File: OUTS.kicad_sch Sheet: /OUTPUTS/ WTMtronics

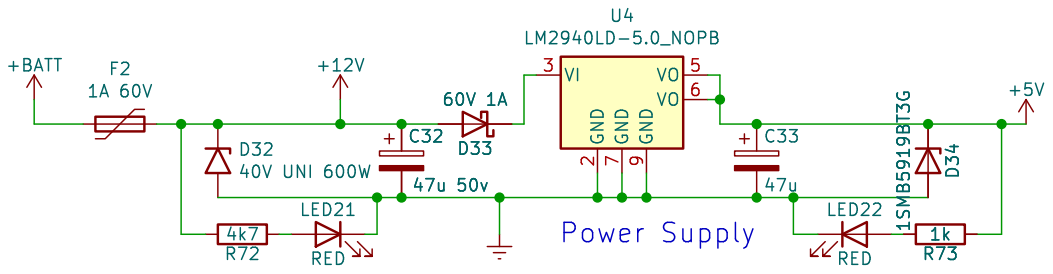
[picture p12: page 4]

2 VI 3 VO 5 VO 6 GND

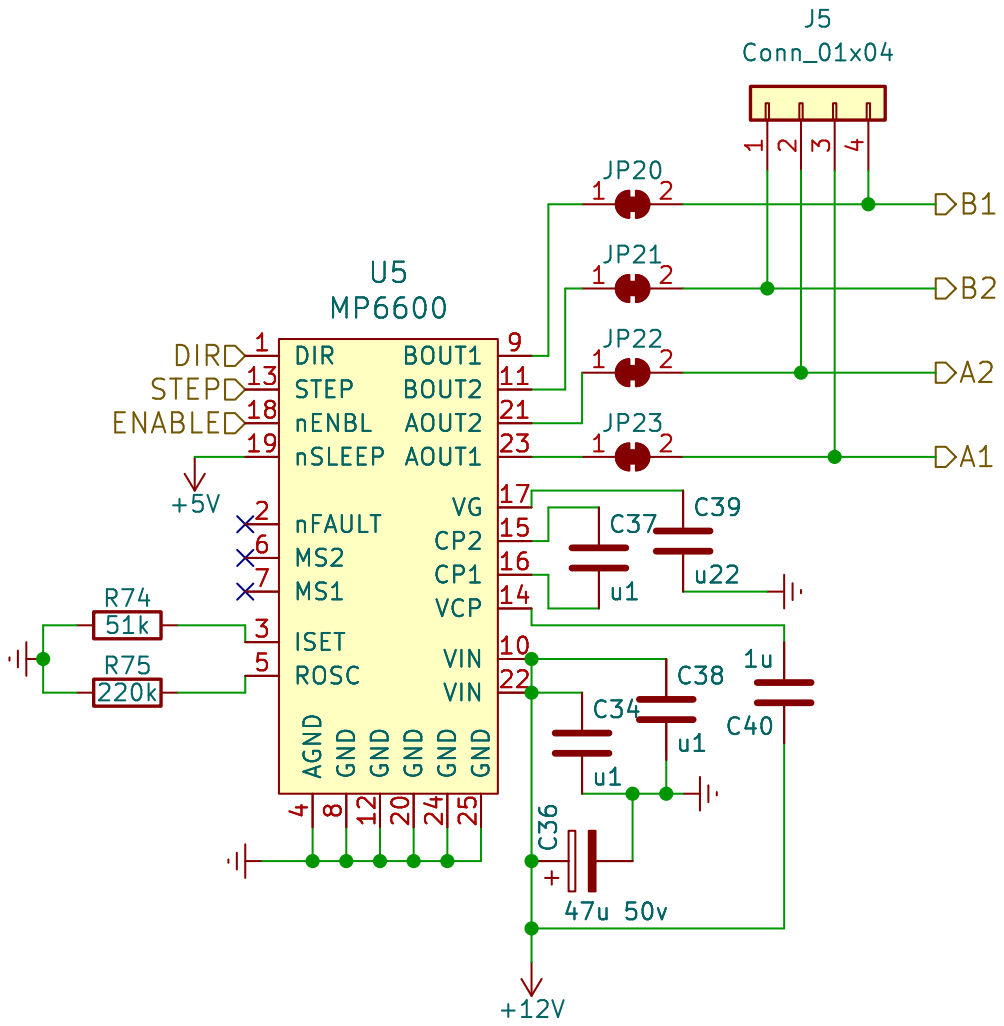
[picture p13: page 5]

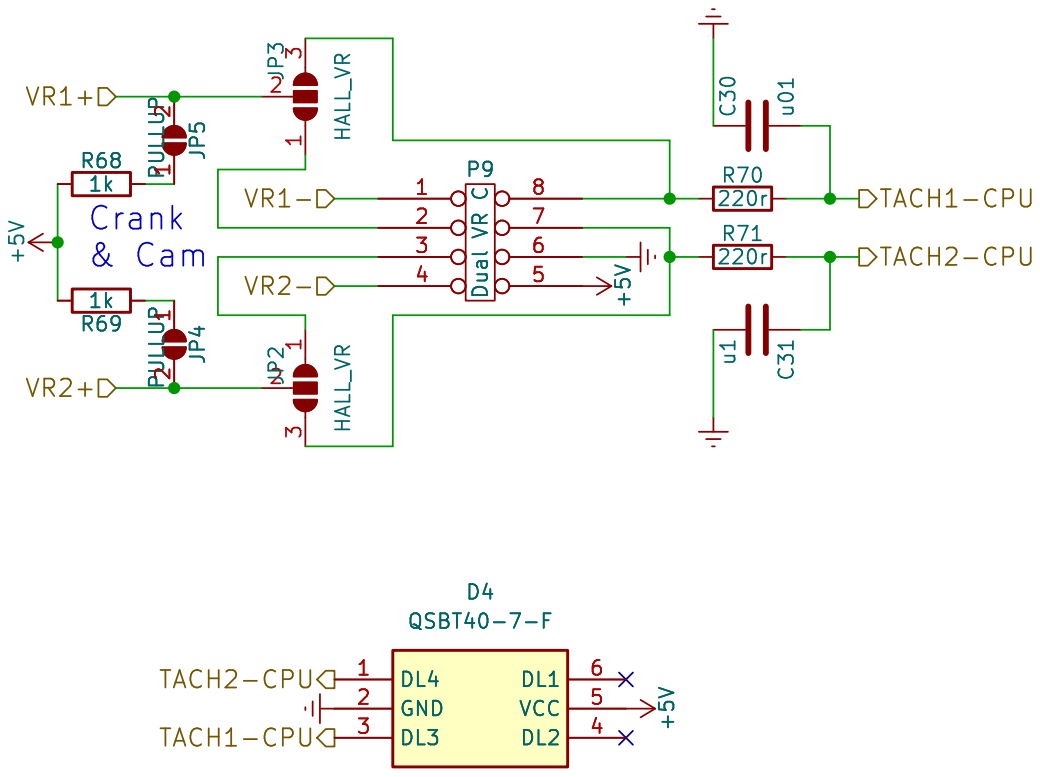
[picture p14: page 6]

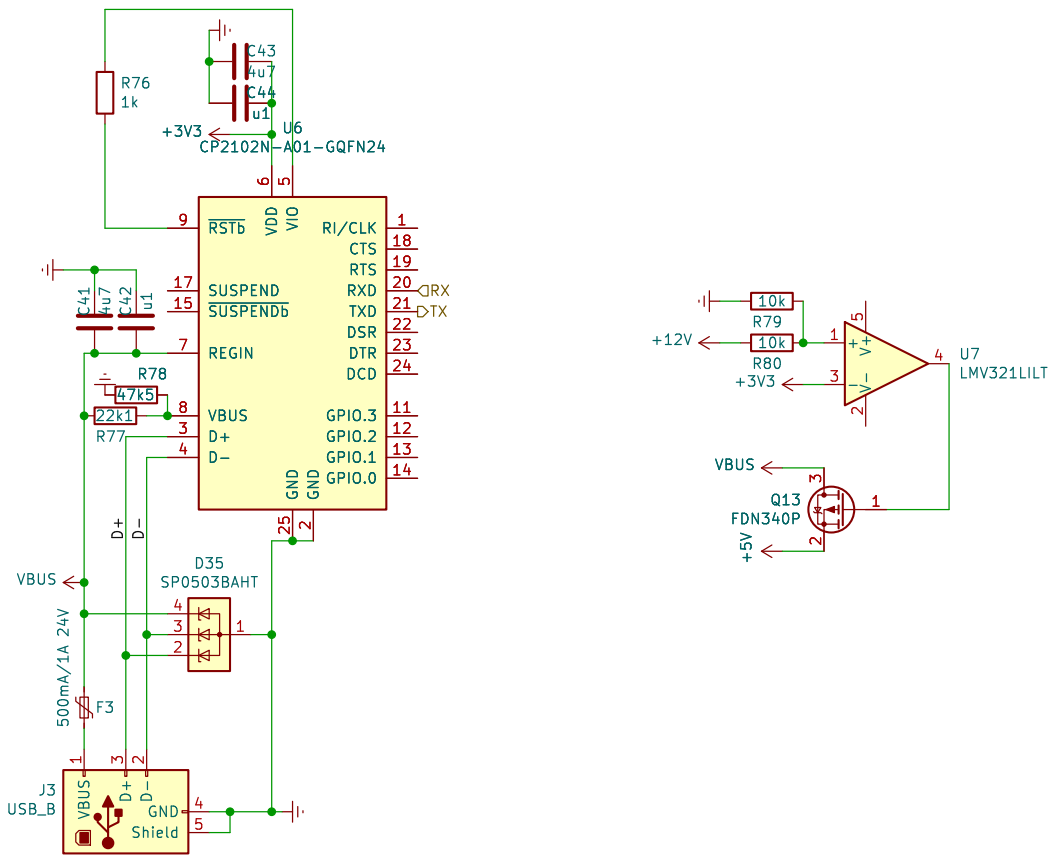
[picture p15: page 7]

File: USB.kicad_sch Sheet: /USB/ WTMtronics

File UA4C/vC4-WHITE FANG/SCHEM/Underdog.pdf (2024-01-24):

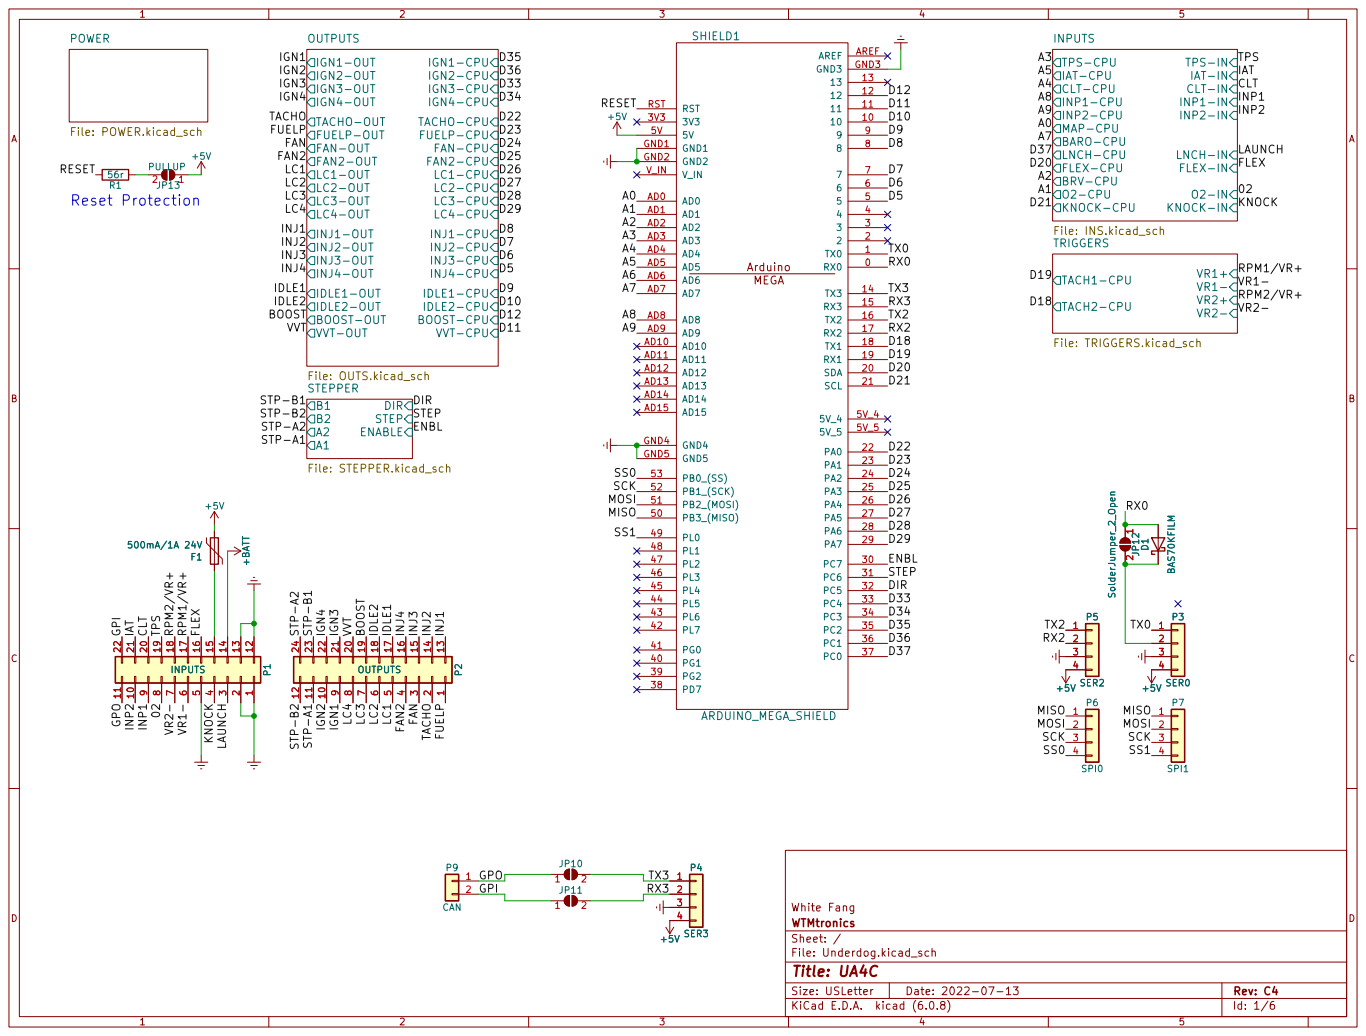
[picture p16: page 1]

File: Underdog.kicad_sch Sheet: / WTMtronics White Fang

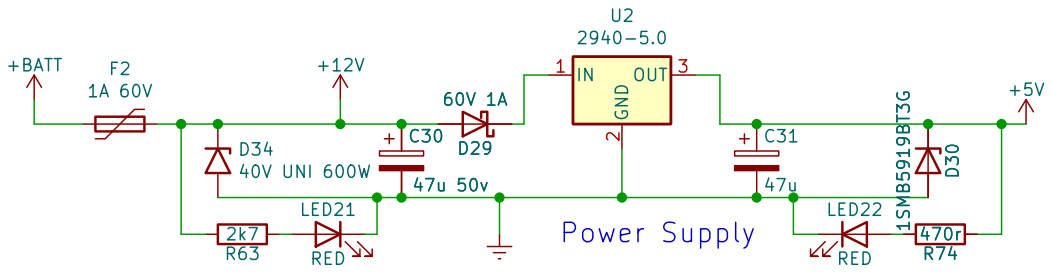
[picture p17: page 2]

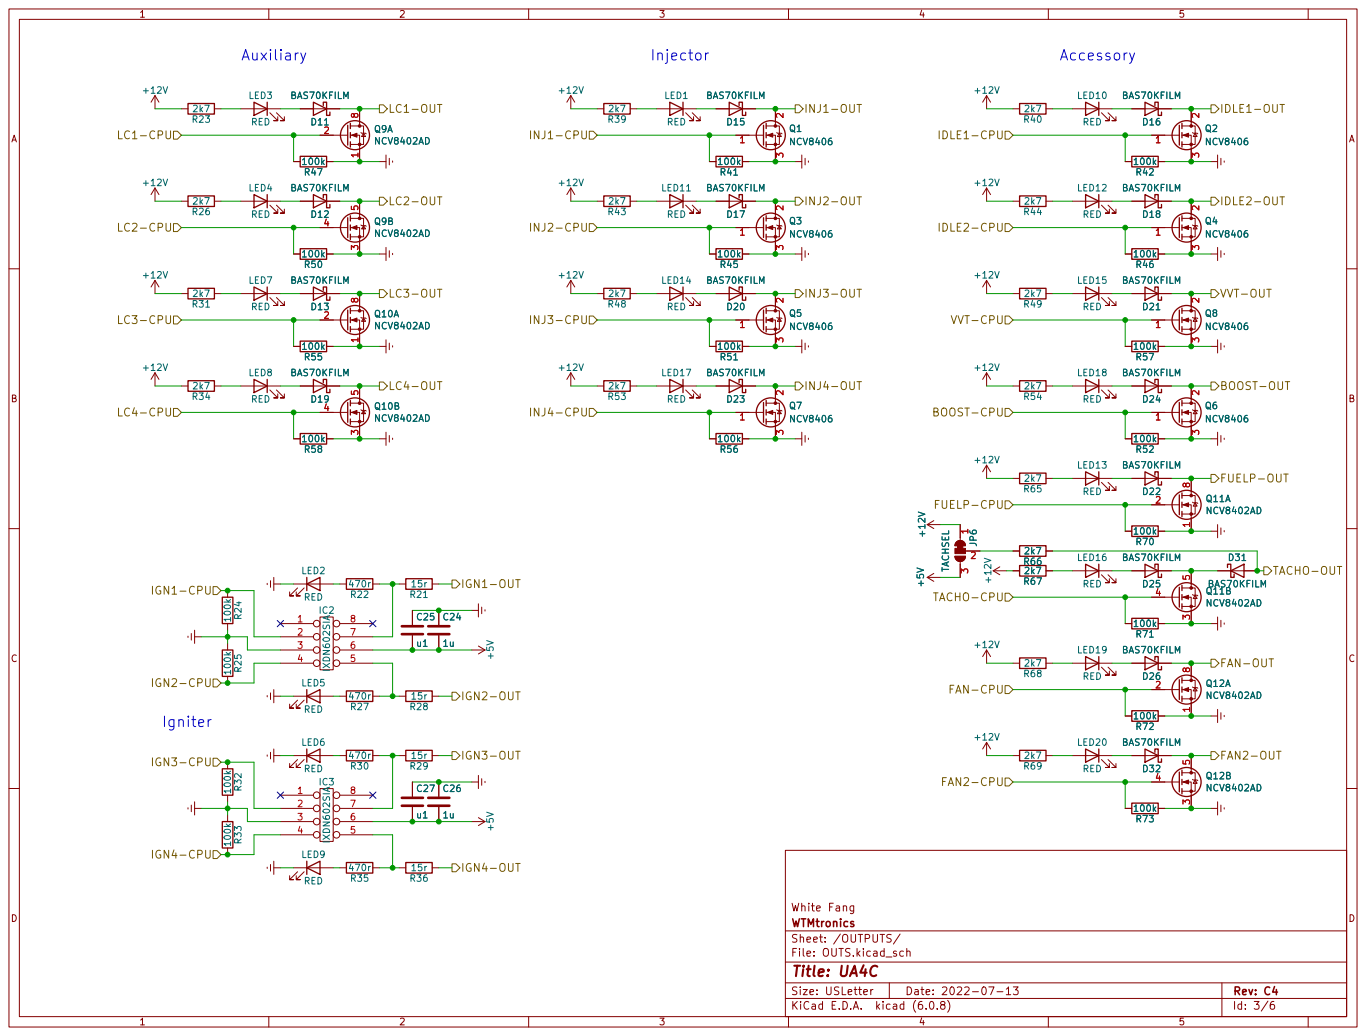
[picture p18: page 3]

File: OUTS.kicad_sch Sheet: /OUTPUTS/ WTMtronics White Fang

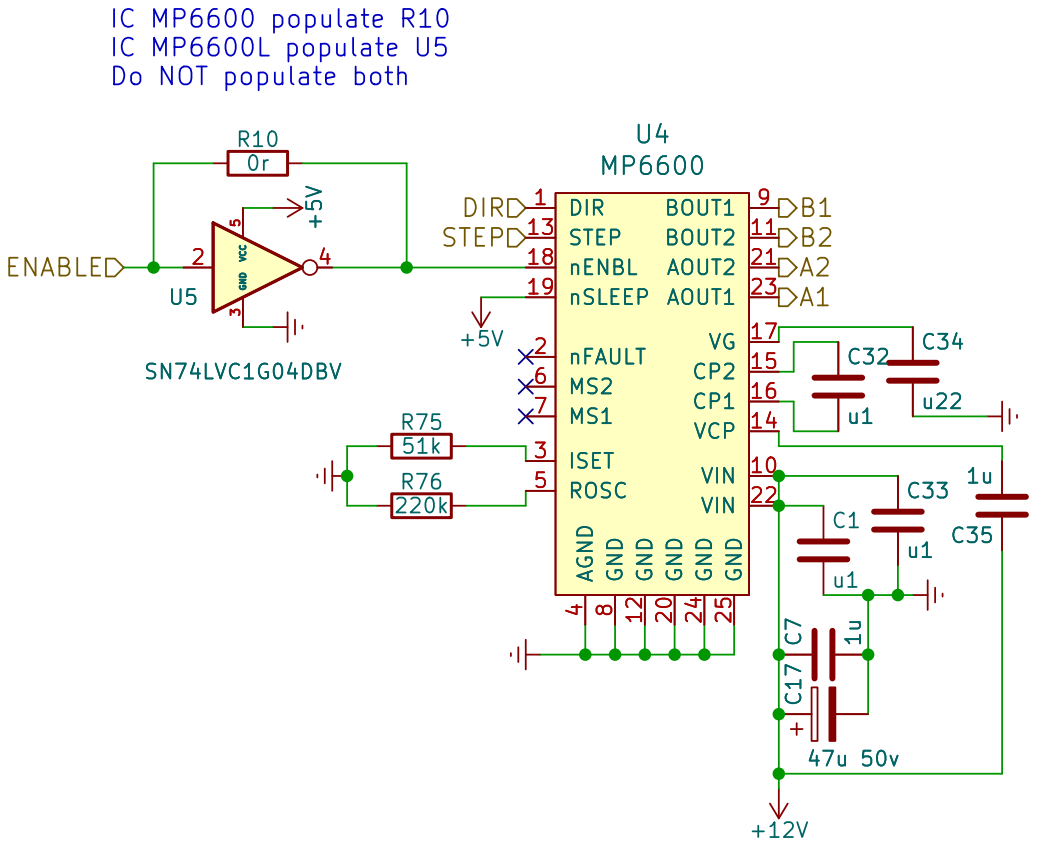
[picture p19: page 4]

IC MP6600 populate R10
IC MP6600L populate U5
File: STEPPER.kicad_sch Sheet: /STEPPER/ WTMtronics White Fang C17

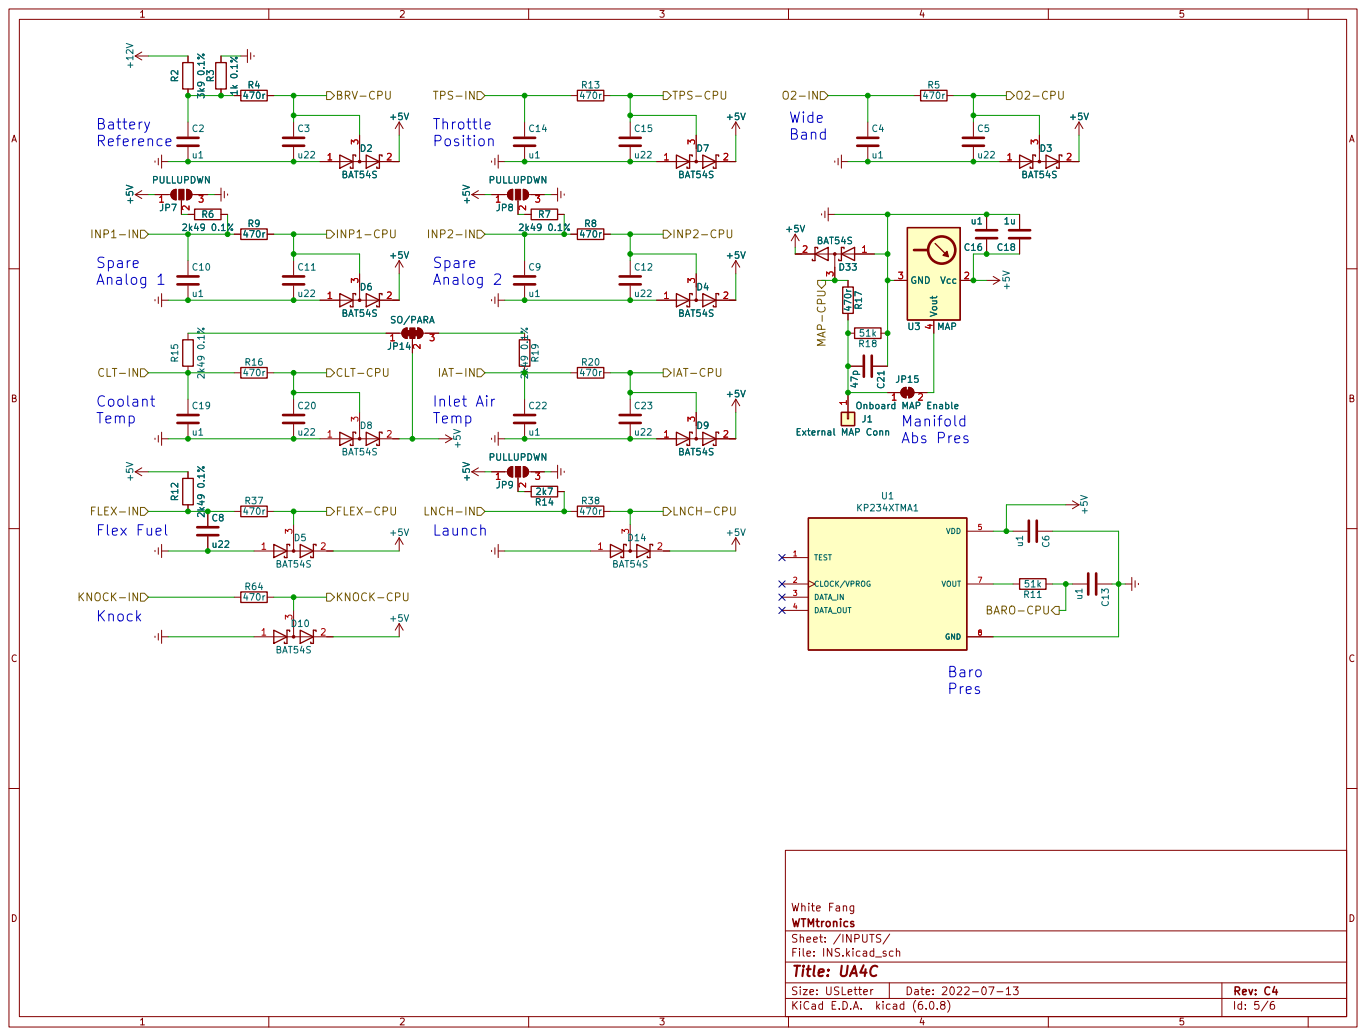
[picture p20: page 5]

File: INS.kicad_sch Sheet: /INPUTS/ WTMtronics White Fang


File: TRIGGERS.kicad_sch Sheet: /TRIGGERS/ WTMtronics White Fang +5V

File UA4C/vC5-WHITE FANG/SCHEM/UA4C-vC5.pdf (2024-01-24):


File: UA4C-vC5.kicad_sch Sheet: / WTMtronics White Fang



File: OUTS.kicad_sch Sheet: /OUTPUTS/ WTMtronics White Fang


IC MP6600 populate R10
IC MP6600L populate U5
File: STEPPER.kicad_sch Sheet: /STEPPER/ WTMtronics White Fang C17


File: INS.kicad_sch Sheet: /INPUTS/ WTMtronics White Fang


File: TRIGGERS.kicad_sch Sheet: /TRIGGERS/ WTMtronics White Fang +5V

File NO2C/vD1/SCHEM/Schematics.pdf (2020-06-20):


Sheet: Inputs and Outputs File: file58BEAE9B.sch TPS-IN
STP-A2 LAUNCH

File: NO2C.sch Sheet: / WTMtronics Shields and Modules


Inputs and Outputs
File: file58BEAE9B.sch Sheet: /Inputs and Outputs/ WTMtronics















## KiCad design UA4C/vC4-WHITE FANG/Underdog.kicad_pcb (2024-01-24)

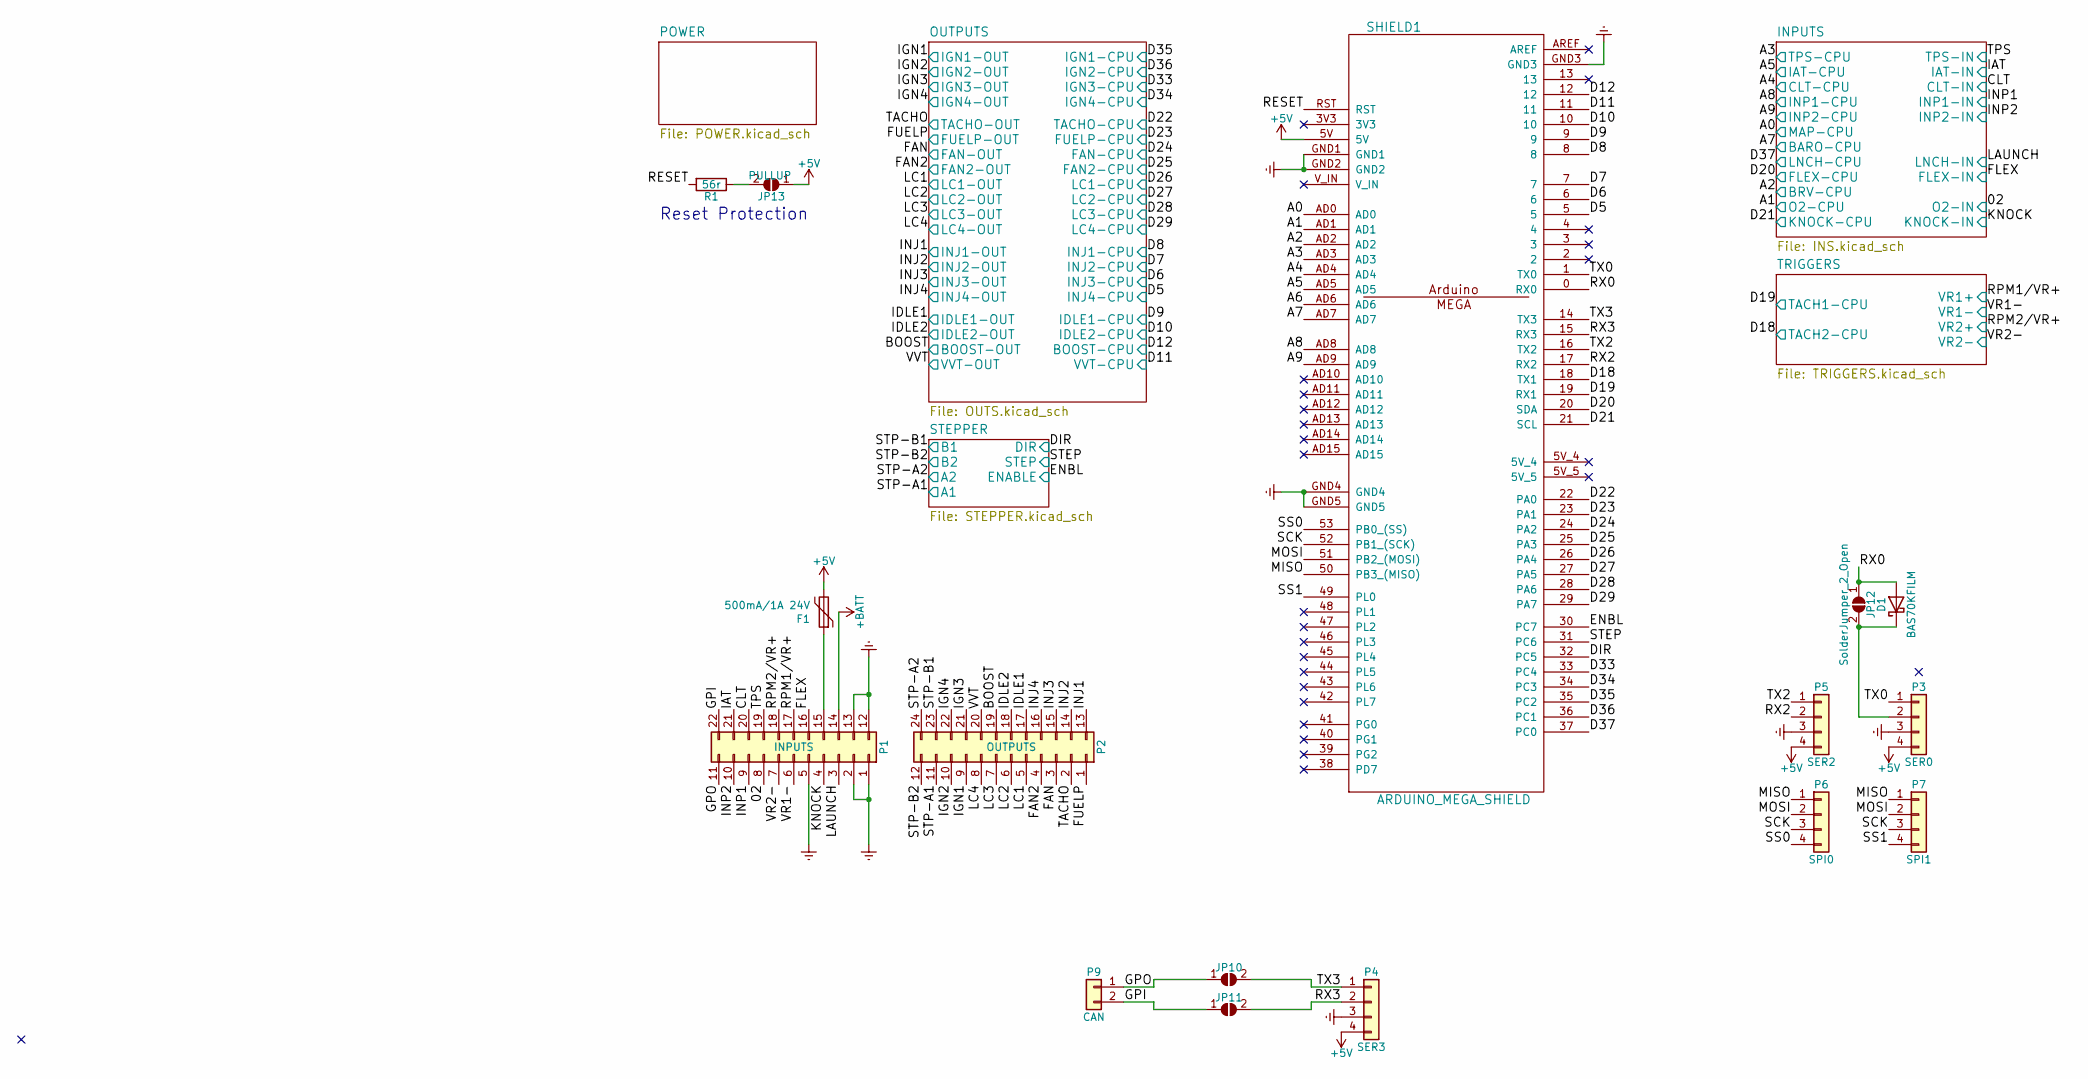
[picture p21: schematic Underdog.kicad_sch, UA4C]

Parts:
D1: BAS70KFILM; D_SOD-523; MPN BAS70-02V-V-G-08
F1: 500mA/1A 24V; Fuse_1206_3216Metric; MPN 0ZCJ0050AF2E
JP10, JP11, JP12: SolderJumper_2_Open; SolderJumper-2_P1.3mm_Open_Pad1.0x1.5mm; MPN DNP
JP13: PULLUP; JPR_2POS_SMLHL; MPN DNP
P1: INPUTS; Molex_Micro-Fit_3.0_43045-2200_2x11_P3.00mm_Horizontal; MPN DNP
P2: OUTPUTS; Molex_Micro-Fit_3.0_43045-2400_2x12_P3.00mm_Horizontal; MPN DNP
P3: SER0; Pin_Header_Straight_1x04_Pitch2.54mm; MPN DNP
P4: SER3; Pin_Header_Straight_1x04_Pitch2.54mm; MPN DNP
P5: SER2; Pin_Header_Straight_1x04_Pitch2.54mm; MPN DNP
P6: SPI0; Pin_Header_Straight_1x04_Pitch2.54mm; MPN DNP
P7: SPI1; Pin_Header_Straight_1x04_Pitch2.54mm; MPN DNP
P9: CAN; PinHeader_1x02_P2.54mm_Vertical; MPN DNP
R1: 56r; R_1206_3216Metric; MPN RK73H2BTTD56R0F
SHIELD1: ARDUINO_MEGA_SHIELD; MPN DNP

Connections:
+5V: F1.2, JP13.1 (A), P3.4, P4.4, P5.4, SHIELD1.5V; also elsewhere on the board
+BATT: P1.14; also elsewhere on the board
/02: P1.8; also elsewhere on the board
/A0: SHIELD1.AD0; also elsewhere on the board
/A1: SHIELD1.AD1; also elsewhere on the board
/A2: SHIELD1.AD2; also elsewhere on the board
/A3: SHIELD1.AD3; also elsewhere on the board
/A4: SHIELD1.AD4; also elsewhere on the board
/A5: SHIELD1.AD5; also elsewhere on the board
/A6: SHIELD1.AD6
/A7: SHIELD1.AD7; also elsewhere on the board
/A8: SHIELD1.AD8; also elsewhere on the board
/A9: SHIELD1.AD9; also elsewhere on the board
/BOOST: P2.19; also elsewhere on the board
/CLT: P1.20; also elsewhere on the board
/D5: SHIELD1.5; also elsewhere on the board
/D6: SHIELD1.6; also elsewhere on the board
/D7: SHIELD1.7; also elsewhere on the board
/D8: SHIELD1.8; also elsewhere on the board
/D9: SHIELD1.9; also elsewhere on the board
/D10: SHIELD1.10; also elsewhere on the board
/D11: SHIELD1.11; also elsewhere on the board
/D12: SHIELD1.12; also elsewhere on the board
/D18: SHIELD1.18 (TX1); also elsewhere on the board
/D19: SHIELD1.19 (RX1); also elsewhere on the board
/D20: SHIELD1.20 (SDA); also elsewhere on the board
/D21: SHIELD1.21 (SCL); also elsewhere on the board
/D22: SHIELD1.22 (PA0); also elsewhere on the board
/D23: SHIELD1.23 (PA1); also elsewhere on the board
/D24: SHIELD1.24 (PA2); also elsewhere on the board
/D25: SHIELD1.25 (PA3); also elsewhere on the board
/D26: SHIELD1.26 (PA4); also elsewhere on the board
/D27: SHIELD1.27 (PA5); also elsewhere on the board
/D28: SHIELD1.28 (PA6); also elsewhere on the board
/D29: SHIELD1.29 (PA7); also elsewhere on the board
/D33: SHIELD1.33 (PC4); also elsewhere on the board
/D34: SHIELD1.34 (PC3); also elsewhere on the board
/D35: SHIELD1.35 (PC2); also elsewhere on the board
/D36: SHIELD1.36 (PC1); also elsewhere on the board
/D37: SHIELD1.37 (PC0); also elsewhere on the board
/DIR: SHIELD1.32 (PC5); also elsewhere on the board
/ENBL: SHIELD1.30 (PC7); also elsewhere on the board
/FAN: P2.3; also elsewhere on the board
/FAN2: P2.4; also elsewhere on the board
/FLEX: P1.16; also elsewhere on the board
/FUELP: P2.1; also elsewhere on the board
/GPI: JP11.1 (A), P1.22, P9.2
/GPO: JP10.1 (A), P1.11, P9.1
/IAT: P1.21; also elsewhere on the board
/IDLE1: P2.17; also elsewhere on the board
/IDLE2: P2.18; also elsewhere on the board
/IGN1: P2.9; also elsewhere on the board
/IGN2: P2.10; also elsewhere on the board
/IGN3: P2.21; also elsewhere on the board
/IGN4: P2.22; also elsewhere on the board
/INJ1: P2.13; also elsewhere on the board
/INJ2: P2.14; also elsewhere on the board
/INJ3: P2.15; also elsewhere on the board
/INJ4: P2.16; also elsewhere on the board
/INP1: P1.9; also elsewhere on the board
/INP2: P1.10; also elsewhere on the board
/KNOCK: P1.4; also elsewhere on the board
/LAUNCH: P1.3; also elsewhere on the board
/LC1: P2.5; also elsewhere on the board
/LC2: P2.6; also elsewhere on the board
/LC3: P2.7; also elsewhere on the board
/LC4: P2.8; also elsewhere on the board
/MISO: P6.1, P7.1, SHIELD1.50 (PB3_(MISO))
/MOSI: P6.2, P7.2, SHIELD1.51 (PB2_(MOSI))
/RESET: R1.2, SHIELD1.RST
/RPM1/VR+: P1.17; also elsewhere on the board
/RPM2/VR+: P1.18; also elsewhere on the board
/RX0: D1.2 (A), JP12.1 (A), SHIELD1.0 (RX0)
/RX2: P5.2, SHIELD1.17 (RX2)
/RX3: JP11.2 (B), P4.2, SHIELD1.15 (RX3)
/SCK: P6.3, P7.3, SHIELD1.52 (PB1_(SCK))
/SS0: P6.4, SHIELD1.53 (PB0_(SS))
/SS1: P7.4, SHIELD1.49 (PL0)
/STEP: SHIELD1.31 (PC6); also elsewhere on the board
/STP-A1: P2.11; also elsewhere on the board
/STP-A2: P2.24; also elsewhere on the board
/STP-B1: P2.23; also elsewhere on the board
/STP-B2: P2.12; also elsewhere on the board
/TACHO: P2.2; also elsewhere on the board
/TPS: P1.19; also elsewhere on the board
/TX0: P3.1, SHIELD1.1 (TX0)
/TX2: P5.1, SHIELD1.16 (TX2)
/TX3: JP10.2 (B), P4.1, SHIELD1.14 (TX3)
/VR1-: P1.6; also elsewhere on the board
/VR2-: P1.7; also elsewhere on the board
/VVT: P2.20; also elsewhere on the board
Earth: P1.1, P1.2, P1.5, P1.12, P1.13, P3.3, P4.3, P5.3, SHIELD1.GND1, SHIELD1.GND2, SHIELD1.GND3, SHIELD1.GND4, SHIELD1.GND5; also elsewhere on the board
unnamed: D1.1 (K), JP12.2 (B), P3.2
unnamed: F1.1, P1.15
unnamed: JP13.2 (B), R1.1

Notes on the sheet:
Reset Protection

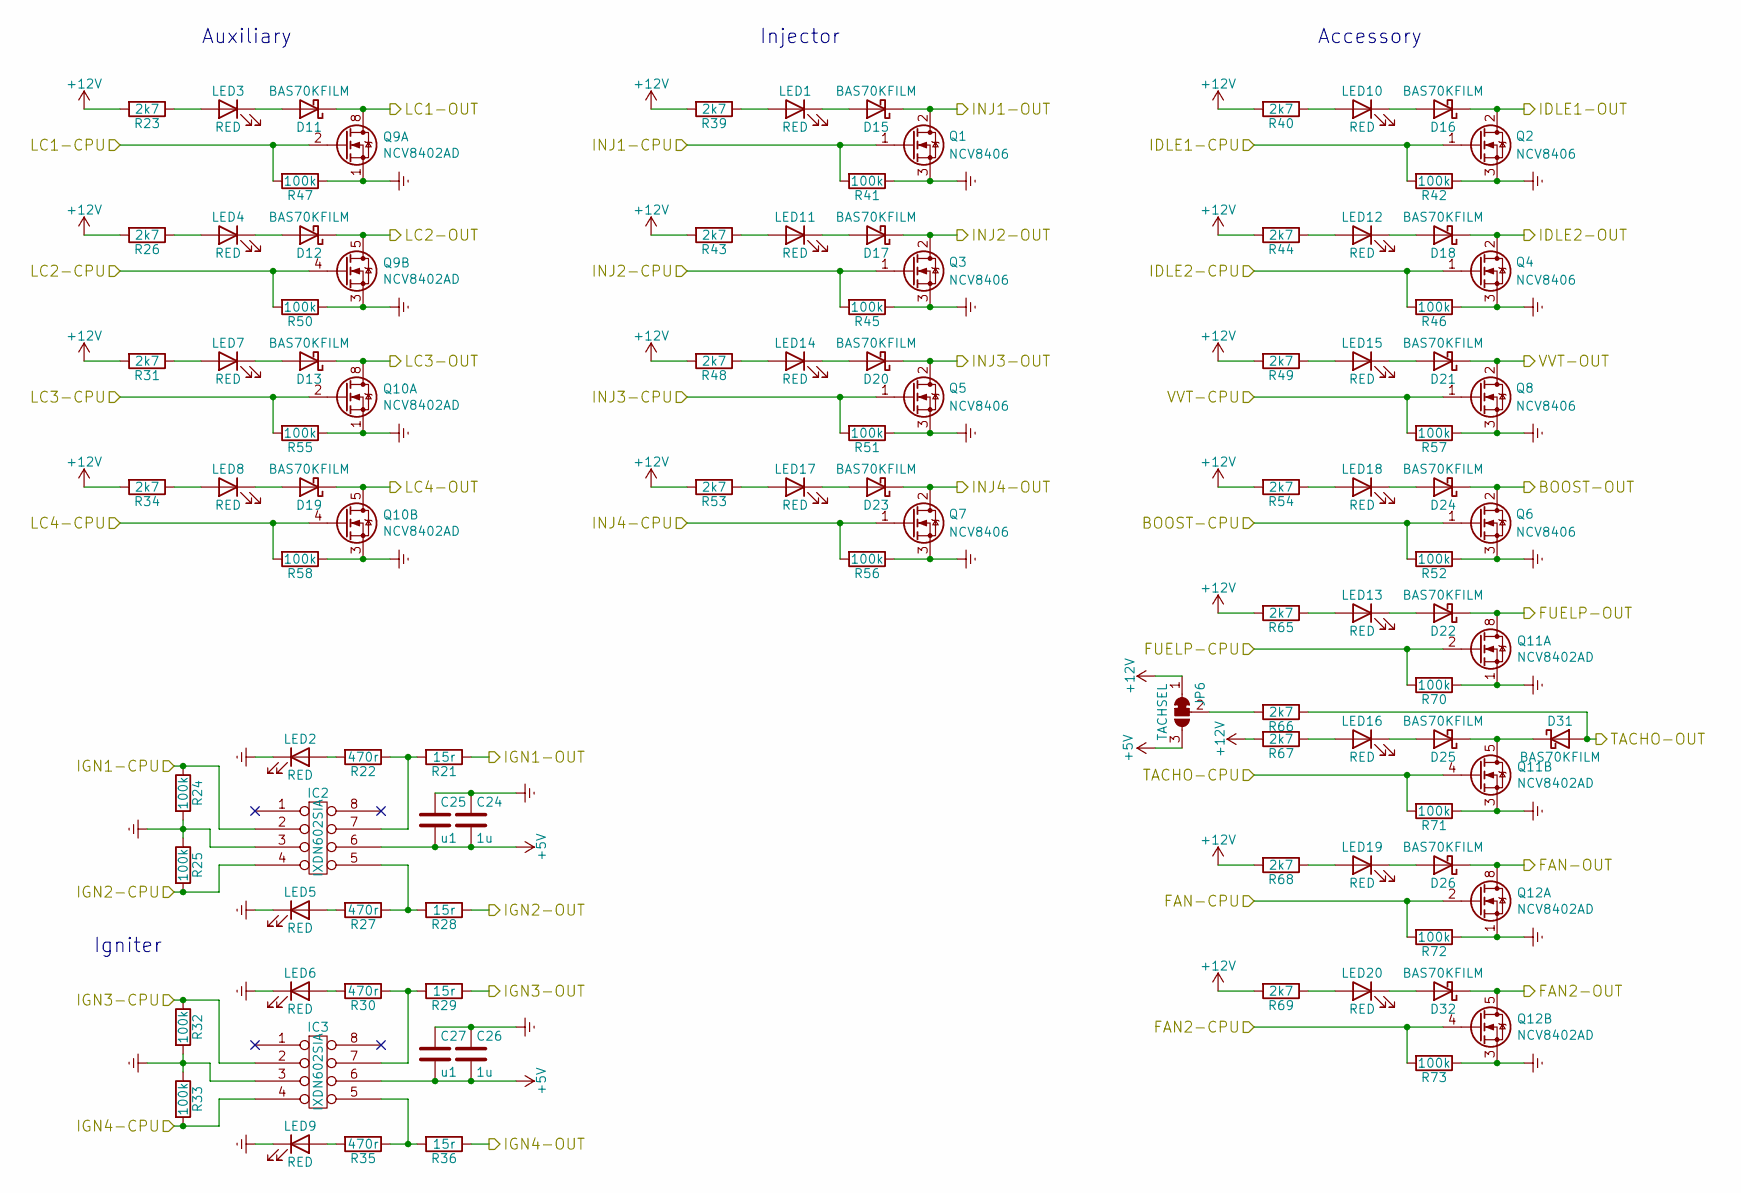
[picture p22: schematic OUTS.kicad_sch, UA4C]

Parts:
C24, C26: 1u; C_0805_2012Metric; MPN CL21B105KBFNNNE
C25, C27: u1; C_0805_2012Metric; MPN CL21B104KBFNNNE
D11, D12, D13, D15, D16, D17, D18, D19, D20, D21, D22, D23, D24, D25, D26, D31, D32: BAS70KFILM; D_SOD-523; MPN BAS70-02V-V-G-08
IC2, IC3: IXDN602SIA; SOIC-8_3.9x4.9mm_P1.27mm; MPN IXDN602SIA
JP6: TACHSEL; SolderJumper-3_P1.3mm_Bridged12_Pad1.0x1.5mm_NumberLabels; MPN DNP
LED1, LED2, LED3, LED4, LED5, LED6, LED7, LED8, LED9, LED10, LED11, LED12, LED13, LED14, LED15, LED16, LED17, LED18, LED19, LED20: RED; LED_0603_1608Metric; MPN SML-310LTT86
Q1, Q2, Q3, Q4, Q5, Q6, Q7, Q8: NCV8406; TO-252-3_TabPin2; MPN NCV8406BDTRKG
Q9, Q10, Q11, Q12: NCV8402AD; SOIC-8_3.9x4.9mm_P1.27mm; MPN NCV8402ADDR2G
R21, R28, R29, R36: 15r; R_2512_6332Metric; MPN RK73H3ATTE15R0F
R22, R27, R30, R35: 470r; R_0805_2012Metric; MPN RK73H2ATTD4700F
R23, R26, R31, R34, R39, R40, R43, R44, R48, R49, R53, R54, R65, R66, R67, R68, R69: 2k7; R_0603_1608Metric; MPN RK73B1JTTD272J
R24, R25, R32, R33, R41, R42, R45, R46, R47, R50, R51, R52, R55, R56, R57, R58, R70, R71, R72, R73: 100k; R_0603_1608Metric; MPN RK73B1JTTD104J

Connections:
+5V: C24.2, C25.2, C26.2, C27.2, IC2.6, IC3.6, JP6.3 (B); also elsewhere on the board
+12V: JP6.1 (A), R23.2, R26.2, R31.2, R34.2, R39.2, R40.2, R43.2, R44.2, R48.2, R49.2, R53.2, R54.2, R65.2, R67.2, R68.2, R69.2; also elsewhere on the board
/BOOST: D24.1 (K), Q6.2 (D); also elsewhere on the board
/D5: Q7.1 (G), R56.2; also elsewhere on the board
/D6: Q5.1 (G), R51.2; also elsewhere on the board
/D7: Q3.1 (G), R45.2; also elsewhere on the board
/D8: Q1.1 (G), R41.2; also elsewhere on the board
/D9: Q2.1 (G), R42.2; also elsewhere on the board
/D10: Q4.1 (G), R46.2; also elsewhere on the board
/D11: Q8.1 (G), R57.2; also elsewhere on the board
/D12: Q6.1 (G), R52.2; also elsewhere on the board
/D22: Q11.4 (G2), R71.2; also elsewhere on the board
/D23: Q11.2 (G1), R70.2; also elsewhere on the board
/D24: Q12.2 (G1), R72.2; also elsewhere on the board
/D25: Q12.4 (G2), R73.2; also elsewhere on the board
/D26: Q9.2 (G1), R47.2; also elsewhere on the board
/D27: Q9.4 (G2), R50.2; also elsewhere on the board
/D28: Q10.2 (G1), R55.2; also elsewhere on the board
/D29: Q10.4 (G2), R58.2; also elsewhere on the board
/D33: IC3.2, R32.1; also elsewhere on the board
/D34: IC3.4, R33.2; also elsewhere on the board
/D35: IC2.2, R24.1; also elsewhere on the board
/D36: IC2.4, R25.2; also elsewhere on the board
/FAN: D26.1 (K), Q12.7 (D1), Q12.8 (D1); also elsewhere on the board
/FAN2: D32.1 (K), Q12.5 (D2), Q12.6 (D2); also elsewhere on the board
/FUELP: D22.1 (K), Q11.7 (D1), Q11.8 (D1); also elsewhere on the board
/IDLE1: D16.1 (K), Q2.2 (D); also elsewhere on the board
/IDLE2: D18.1 (K), Q4.2 (D); also elsewhere on the board
/IGN1: R21.1; also elsewhere on the board
/IGN2: R28.1; also elsewhere on the board
/IGN3: R29.1; also elsewhere on the board
/IGN4: R36.1; also elsewhere on the board
/INJ1: D15.1 (K), Q1.2 (D); also elsewhere on the board
/INJ2: D17.1 (K), Q3.2 (D); also elsewhere on the board
/INJ3: D20.1 (K), Q5.2 (D); also elsewhere on the board
/INJ4: D23.1 (K), Q7.2 (D); also elsewhere on the board
/LC1: D11.1 (K), Q9.7 (D1), Q9.8 (D1); also elsewhere on the board
/LC2: D12.1 (K), Q9.5 (D2), Q9.6 (D2); also elsewhere on the board
/LC3: D13.1 (K), Q10.7 (D1), Q10.8 (D1); also elsewhere on the board
/LC4: D19.1 (K), Q10.5 (D2), Q10.6 (D2); also elsewhere on the board
/TACHO: D31.2 (A), R66.1; also elsewhere on the board
/VVT: D21.1 (K), Q8.2 (D); also elsewhere on the board
Earth: C24.1, C25.1, C26.1, C27.1, IC2.3, IC3.3, LED2.1 (K), LED5.1 (K), LED6.1 (K), LED9.1 (K), Q1.3 (S), Q2.3 (S), Q3.3 (S), Q4.3 (S), Q5.3 (S), Q6.3 (S), Q7.3 (S), Q8.3 (S), Q9.1 (S1), Q9.3 (S2), Q10.1 (S1), Q10.3 (S2), Q11.1 (S1), Q11.3 (S2), Q12.1 (S1), Q12.3 (S2), R24.2, R25.1, R32.2, R33.1, R41.1, R42.1, R45.1, R46.1, R47.1, R50.1, R51.1, R52.1, R55.1, R56.1, R57.1, R58.1, R70.1, R71.1, R72.1, R73.1; also elsewhere on the board
unnamed: D11.2 (A), LED3.1 (K)
unnamed: D12.2 (A), LED4.1 (K)
unnamed: D13.2 (A), LED7.1 (K)
unnamed: D15.2 (A), LED1.1 (K)
unnamed: D16.2 (A), LED10.1 (K)
unnamed: D17.2 (A), LED11.1 (K)
unnamed: D18.2 (A), LED12.1 (K)
unnamed: D19.2 (A), LED8.1 (K)
unnamed: D20.2 (A), LED14.1 (K)
unnamed: D21.2 (A), LED15.1 (K)
unnamed: D22.2 (A), LED13.1 (K)
unnamed: D23.2 (A), LED17.1 (K)
unnamed: D24.2 (A), LED18.1 (K)
unnamed: D25.1 (K), D31.1 (K), Q11.5 (D2), Q11.6 (D2)
unnamed: D25.2 (A), LED16.1 (K)
unnamed: D26.2 (A), LED19.1 (K)
unnamed: D32.2 (A), LED20.1 (K)
unnamed: IC2.5, R27.1, R28.2
unnamed: IC2.7, R21.2, R22.1
unnamed: IC3.5, R35.1, R36.2
unnamed: IC3.7, R29.2, R30.1
unnamed: JP6.2 (C), R66.2
unnamed: LED1.2 (A), R39.1
unnamed: LED2.2 (A), R22.2
unnamed: LED3.2 (A), R23.1
unnamed: LED4.2 (A), R26.1
unnamed: LED5.2 (A), R27.2
unnamed: LED6.2 (A), R30.2
unnamed: LED7.2 (A), R31.1
unnamed: LED8.2 (A), R34.1
unnamed: LED9.2 (A), R35.2
unnamed: LED10.2 (A), R40.1
unnamed: LED11.2 (A), R43.1
unnamed: LED12.2 (A), R44.1
unnamed: LED13.2 (A), R65.1
unnamed: LED14.2 (A), R48.1
unnamed: LED15.2 (A), R49.1
unnamed: LED16.2 (A), R67.1
unnamed: LED17.2 (A), R53.1
unnamed: LED18.2 (A), R54.1
unnamed: LED19.2 (A), R68.1
unnamed: LED20.2 (A), R69.1

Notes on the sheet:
Accessory
Auxiliary
Injector
Igniter

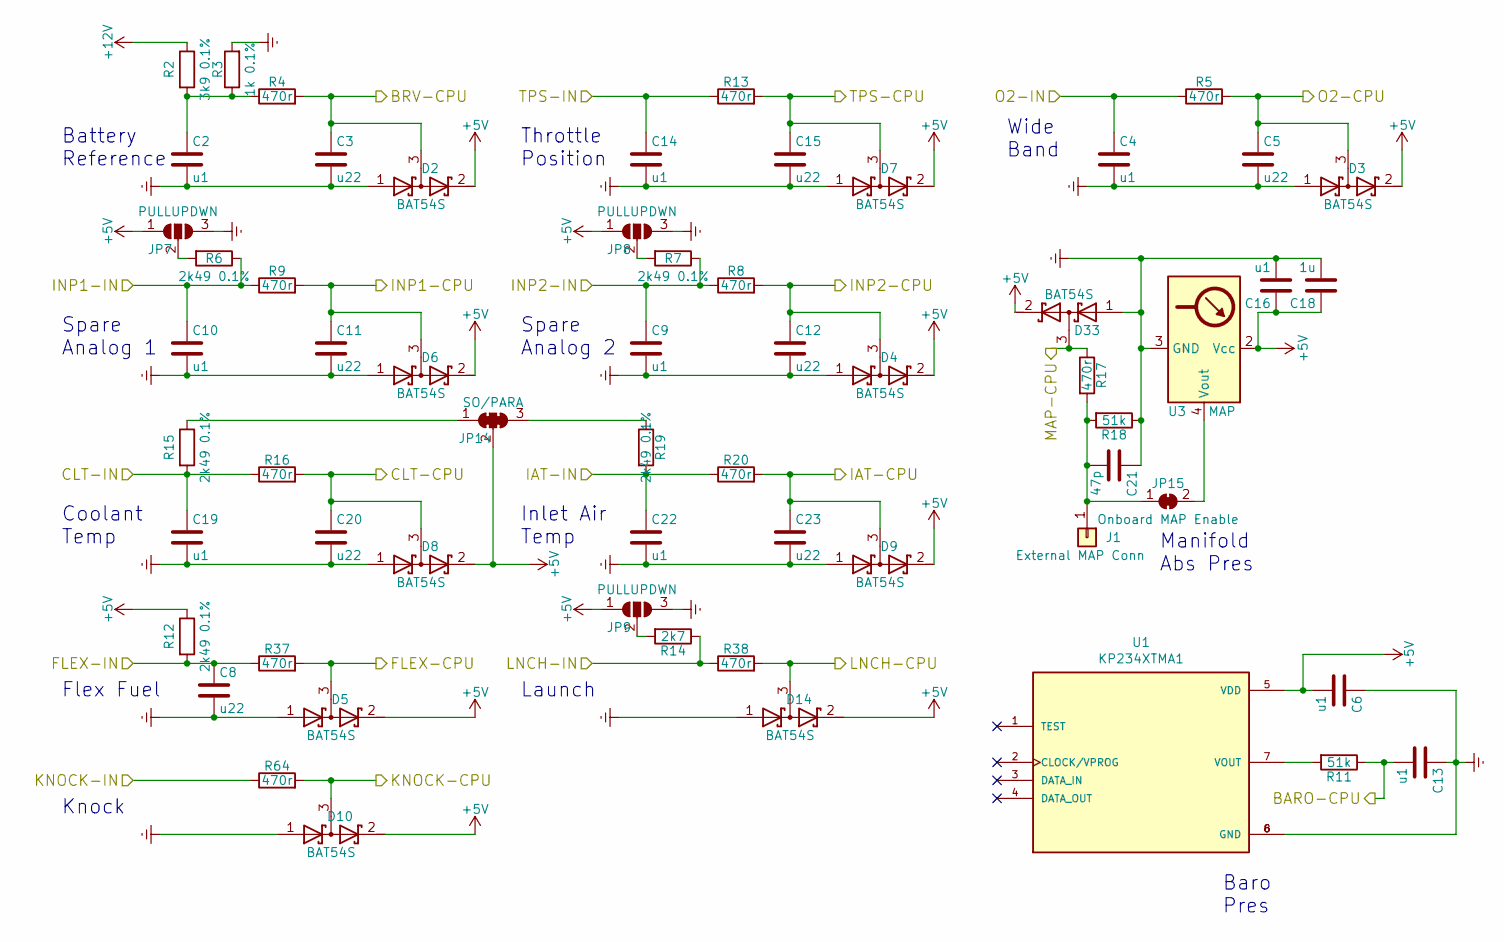
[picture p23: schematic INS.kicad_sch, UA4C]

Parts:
C2, C4, C6, C9, C10, C13, C14, C16, C19, C22: u1; C_0805_2012Metric; MPN CL21B104KBFNNNE
C3, C5, C8, C11, C12, C15, C20, C23: u22; C_0805_2012Metric; MPN CL21B224KBFNNNE
C18: 1u; C_0805_2012Metric; MPN CL21B105KBFNNNE
C21: 47p; C_0805_2012Metric; MPN CL21C470JBANNNC
D2, D3, D4, D5, D6, D7, D8, D9, D10, D14, D33: BAT54S; SOT-23; MPN BAT54S,215
J1: External MAP Conn; SolderWirePad_single_1mmDrill; MPN DNP
JP7, JP8, JP9: PULLUPDWN; SolderJumper-3_P1.3mm_Open_Pad1.0x1.5mm_NumberLabels; MPN DNP
JP14: SO/PARA; SolderJumper-3_P1.3mm_Bridged123_Pad1.0x1.5mm_NumberLabels; MPN DNP
JP15: Onboard MAP Enable; SolderJumper-2_P1.3mm_Bridged_Pad1.0x1.5mm; MPN DNP
R2: 3k9 0.1%; R_0805_2012Metric; MPN ERA6AEB392V
R3: 1k 0.1%; R_0805_2012Metric; MPN ERA6AEB102V
R4, R5, R8, R9, R13, R16, R17, R20, R37, R38, R64: 470r; R_0805_2012Metric; MPN RK73H2ATTD4700F
R6, R7, R12, R15, R19: 2k49 0.1%; R_0805_2012Metric; MPN ERA6AEB2491V
R11, R18: 51k; R_0805_2012Metric; MPN RK73H2ATTD5102F
R14: 2k7; R_0603_1608Metric; MPN RK73B1JTTD272J
U1: KP234XTMA1; XDCR_KP234XTMA1; PARTREV 1.0
U3: MAP; NXP_Pressure_Sensor_SSOP; MPN MPXH6400AC6U

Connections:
+5V: C6.2, C16.1, C18.1, D2.2 (K), D3.2 (K), D4.2 (K), D5.2 (K), D6.2 (K), D7.2 (K), D8.2 (K), D9.2 (K), D10.2 (K), D14.2 (K), D33.2 (K), JP7.1 (A), JP8.1 (A), JP9.1 (A), JP14.2 (C), R12.1, U1.5 (VDD), U3.2 (Vcc); also elsewhere on the board
+12V: R2.1; also elsewhere on the board
/02: C4.1, R5.1; also elsewhere on the board
/A0: D33.3 (common), R17.1; also elsewhere on the board
/A1: C5.1, D3.3 (common), R5.2; also elsewhere on the board
/A2: C3.1, D2.3 (common), R4.2; also elsewhere on the board
/A3: C15.1, D7.3 (common), R13.2; also elsewhere on the board
/A4: C20.1, D8.3 (common), R16.2; also elsewhere on the board
/A5: C23.1, D9.3 (common), R20.2; also elsewhere on the board
/A7: C13.2, R11.1; also elsewhere on the board
/A8: C11.1, D6.3 (common), R9.2; also elsewhere on the board
/A9: C12.1, D4.3 (common), R8.2; also elsewhere on the board
/CLT: C19.1, R15.2, R16.1; also elsewhere on the board
/D20: D5.3 (common), R37.2; also elsewhere on the board
/D21: D10.3 (common), R64.2; also elsewhere on the board
/D37: D14.3 (common), R38.2; also elsewhere on the board
/FLEX: C8.1, R12.2, R37.1; also elsewhere on the board
/IAT: C22.1, R19.2, R20.1; also elsewhere on the board
/INP1: C10.1, R6.1, R9.1; also elsewhere on the board
/INP2: C9.1, R7.1, R8.1; also elsewhere on the board
/KNOCK: R64.1; also elsewhere on the board
/LAUNCH: R14.1, R38.1; also elsewhere on the board
/TPS: C14.1, R13.1; also elsewhere on the board
Earth: C2.2, C3.2, C4.2, C5.2, C6.1, C8.2, C9.2, C10.2, C11.2, C12.2, C13.1, C14.2, C15.2, C16.2, C18.2, C19.2, C20.2, C21.1, C22.2, C23.2, D2.1 (A), D3.1 (A), D4.1 (A), D5.1 (A), D6.1 (A), D7.1 (A), D8.1 (A), D9.1 (A), D10.1 (A), D14.1 (A), D33.1 (A), JP7.3 (B), JP8.3 (B), JP9.3 (B), R3.2, R18.1, U1.6 (GND), U1.8 (GND), U3.3 (GND); also elsewhere on the board
unnamed: C2.1, R2.2, R3.1, R4.1
unnamed: C21.2, J1.1, JP15.1 (A), R17.2, R18.2
unnamed: JP7.2 (C), R6.2
unnamed: JP8.2 (C), R7.2
unnamed: JP9.2 (C), R14.2
unnamed: JP14.1 (A), R15.1
unnamed: JP14.3 (B), R19.1
unnamed: JP15.2 (B), U3.4 (Vout)
unnamed: R11.2, U1.7 (VOUT)

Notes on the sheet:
Throttle Position
Knock
Inlet Air Temp
Wide Band
Flex Fuel
Battery Reference
Coolant Temp
Launch
Manifold Abs Pres
Spare Analog 1
Spare Analog 2
Baro Pres

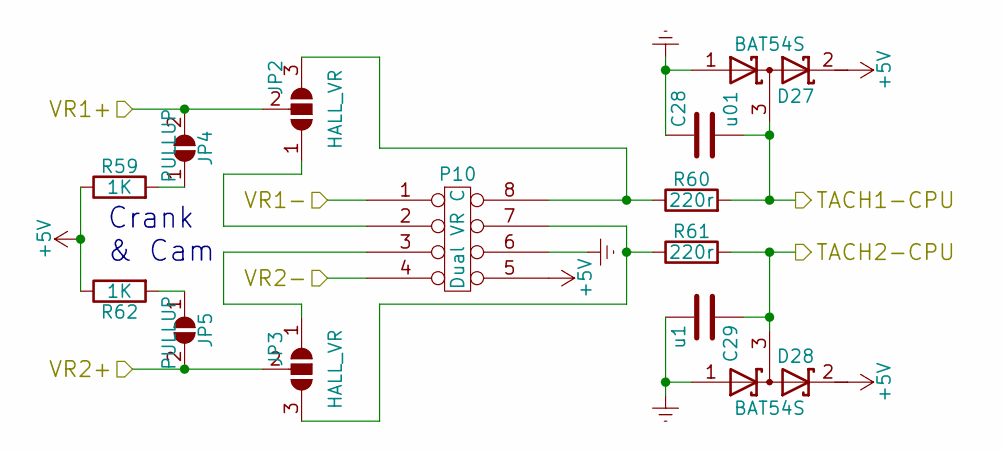
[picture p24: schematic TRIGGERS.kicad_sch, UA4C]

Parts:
C28: u01; C_0805_2012Metric; MPN CL21B103KBCNNNC
C29: u1; C_0805_2012Metric; MPN CL21B104KBFNNNE
D27, D28: BAT54S; SOT-23; MPN BAT54S,215
JP2, JP3: HALL_VR; JPR_3POS_SMLHL; MPN DNP
JP4, JP5: PULLUP; JPR_2POS_SMLHL; MPN DNP
P10: Dual VR C; DIP-8_W7.62mm_Socket; MPN DNP
R59, R62: 1K; R_0805_2012Metric; MPN RK73H2ATTD1001F
R60, R61: 220r; R_0805_2012Metric; MPN RK73H2ATTD2200F

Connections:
+5V: D27.2 (K), D28.2 (K), P10.5, R59.1, R62.1; also elsewhere on the board
/D18: C29.1, D28.3 (common), R61.2; also elsewhere on the board
/D19: C28.2, D27.3 (common), R60.2; also elsewhere on the board
/RPM1/VR+: JP2.2 (C), JP4.2 (B); also elsewhere on the board
/RPM2/VR+: JP3.2 (C), JP5.2 (B); also elsewhere on the board
/VR1-: P10.1; also elsewhere on the board
/VR2-: P10.4; also elsewhere on the board
Earth: C28.1, C29.2, D27.1 (A), D28.1 (A), P10.6; also elsewhere on the board
unnamed: JP2.1 (A), P10.2
unnamed: JP2.3 (B), P10.8, R60.1
unnamed: JP3.1 (A), P10.3
unnamed: JP3.3 (B), P10.7, R61.1
unnamed: JP4.1 (A), R59.2
unnamed: JP5.1 (A), R62.2

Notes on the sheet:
Crank & Cam

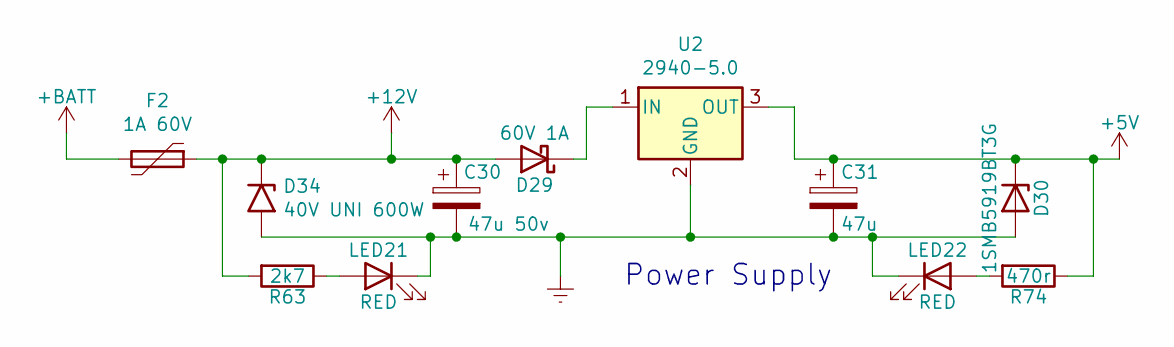
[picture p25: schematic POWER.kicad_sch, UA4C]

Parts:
C30: 47u 50v; CP_Elec_6.3x5.4; MPN EEE-FT1H470AL
C31: 47u; CP_EIA-3216-18_Kemet-A; MPN T55A476M6R3C0200
D29: 60V 1A; D_SMA; MPN B160-E3/61T
D30: 1SMB5919BT3G; D_SMB; MPN 1SMB5919BT3G
D34: 40V UNI 600W; D_SMB; MPN SMBJ40A
F2: 1A 60V; Fuse_2920_7451Metric_Castellated; MPN 0ZCF0100AF2A
LED21, LED22: RED; LED_0603_1608Metric; MPN SML-310LTT86
R63: 2k7; R_0603_1608Metric; MPN RK73B1JTTD272J
R74: 470r; R_0805_2012Metric; MPN RK73H2ATTD4700F
U2: 2940-5.0; TO-252-3_TabPin2

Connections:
+5V: C31.1, D30.1 (K), R74.1, U2.3 (OUT); also elsewhere on the board
+12V: C30.1, D29.2 (A), D34.1 (A1), F2.1, R63.2; also elsewhere on the board
+BATT: F2.2; also elsewhere on the board
Earth: C30.2, C31.2, D30.2 (A), D34.2 (A2), LED21.1 (K), LED22.1 (K), U2.2 (GND); also elsewhere on the board
unnamed: D29.1 (K), U2.1 (IN)
unnamed: LED21.2 (A), R63.1
unnamed: LED22.2 (A), R74.2

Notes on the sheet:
Power Supply

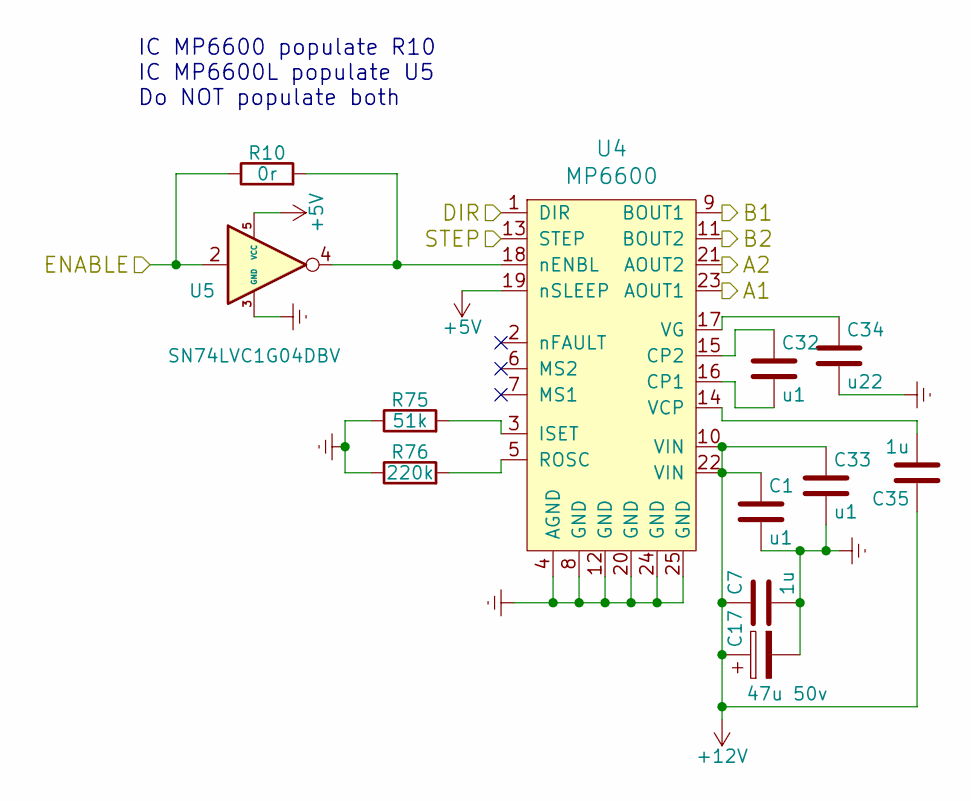
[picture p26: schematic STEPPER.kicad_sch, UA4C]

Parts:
C1, C32, C33: u1; C_0805_2012Metric; MPN CL21B104KBFNNNE
C7, C35: 1u; C_0805_2012Metric; MPN CL21B105KBFNNNE
C17: 47u 50v; CP_Elec_6.3x5.4; MPN EEE-FT1H470AL
C34: u22; C_0805_2012Metric; MPN CL21B224KBFNNNE
R10: 0r; R_0805_2012Metric
R75: 51k; R_0805_2012Metric; MPN RK73H2ATTD5102F
R76: 220k; R_0805_2012Metric; MPN RK73H2ATTD2203F
U4: MP6600; QFN-24-1EP_4x4mm_P0.5mm_EP2.7x2.7mm_ThermalVias; MPN MP6600GR-Z
U5: SN74LVC1G04DBV; SOT-23-5

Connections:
+5V: U4.19 (nSLEEP), U5.5 (VCC); also elsewhere on the board
+12V: C1.1, C7.1, C17.1, C33.1, C35.1, U4.10 (VIN), U4.22 (VIN); also elsewhere on the board
/DIR: U4.1 (DIR); also elsewhere on the board
/ENBL: R10.1, U5.2; also elsewhere on the board
/STEP: U4.13 (STEP); also elsewhere on the board
/STP-A1: U4.23 (AOUT1); also elsewhere on the board
/STP-A2: U4.21 (AOUT2); also elsewhere on the board
/STP-B1: U4.9 (BOUT1); also elsewhere on the board
/STP-B2: U4.11 (BOUT2); also elsewhere on the board
Earth: C1.2, C7.2, C17.2, C33.2, C34.2, R75.1, R76.1, U4.4 (AGND), U4.8 (GND), U4.12 (GND), U4.20 (GND), U4.24 (GND), U4.25 (GND), U5.3 (GND); also elsewhere on the board
unnamed: C32.1, U4.15 (CP2)
unnamed: C32.2, U4.16 (CP1)
unnamed: C34.1, U4.17 (VG)
unnamed: C35.2, U4.14 (VCP)
unnamed: R75.2, U4.3 (ISET)
unnamed: R76.2, U4.5 (ROSC)
unnamed: R10.2, U4.18 (nENBL), U5.4

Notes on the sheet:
IC MP6600 populate R10 IC MP6600L populate U5 Do NOT populate both

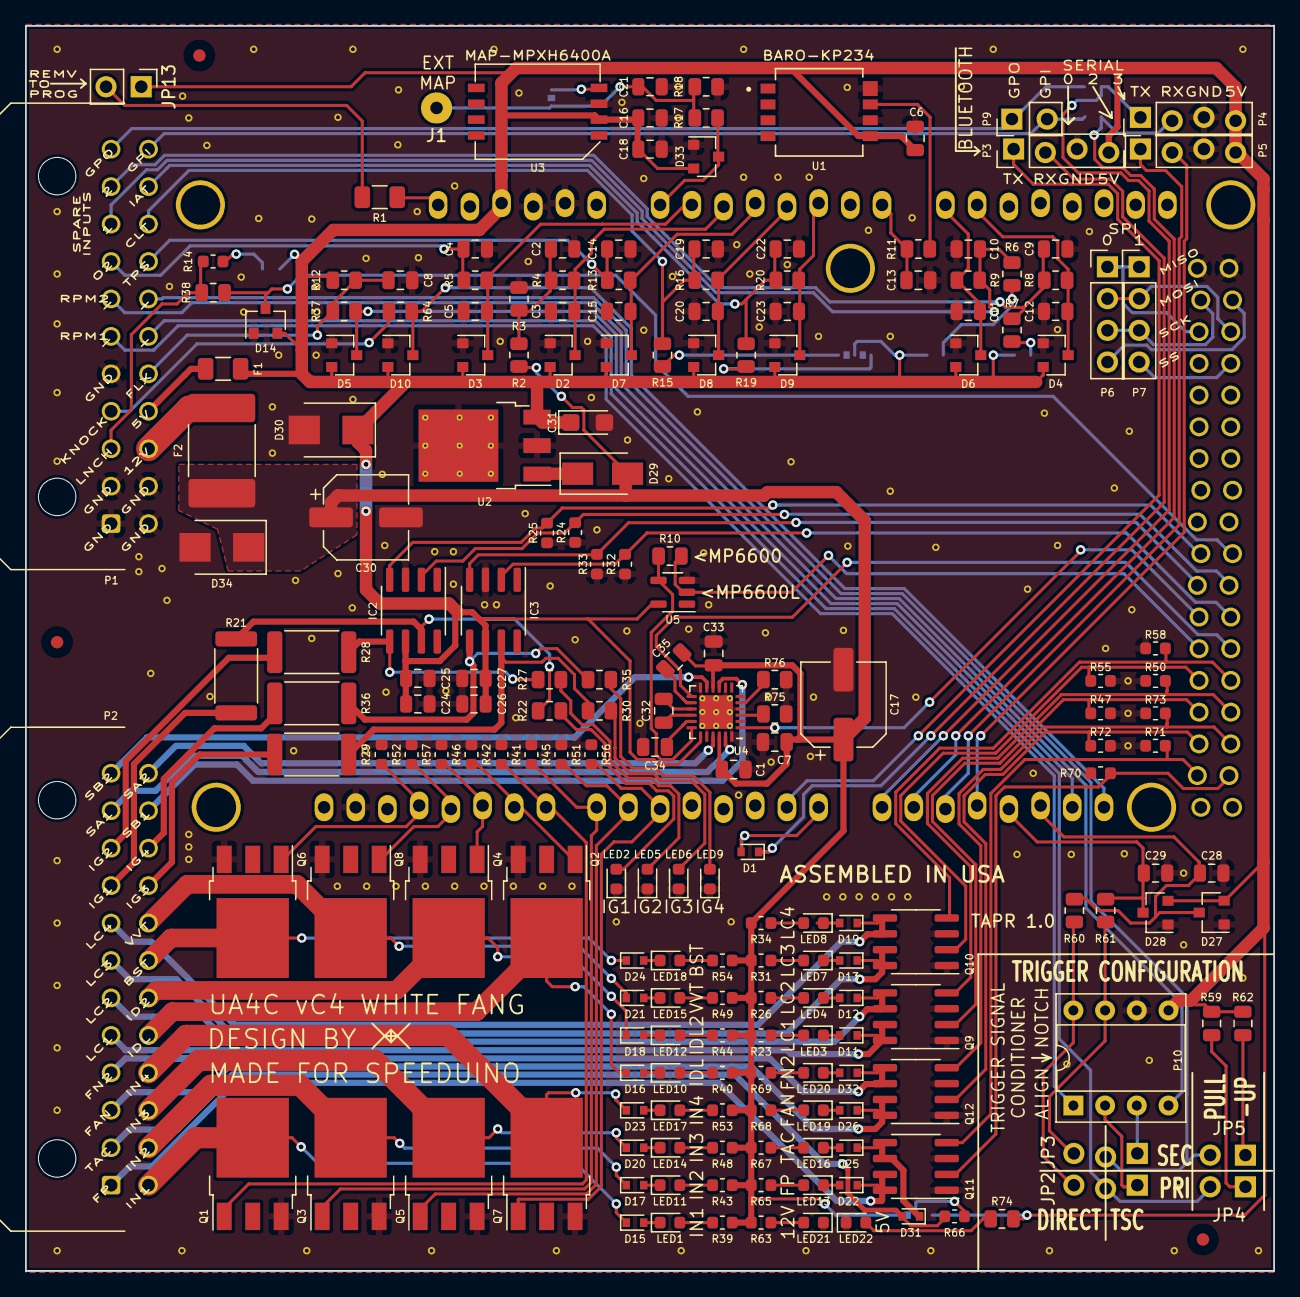
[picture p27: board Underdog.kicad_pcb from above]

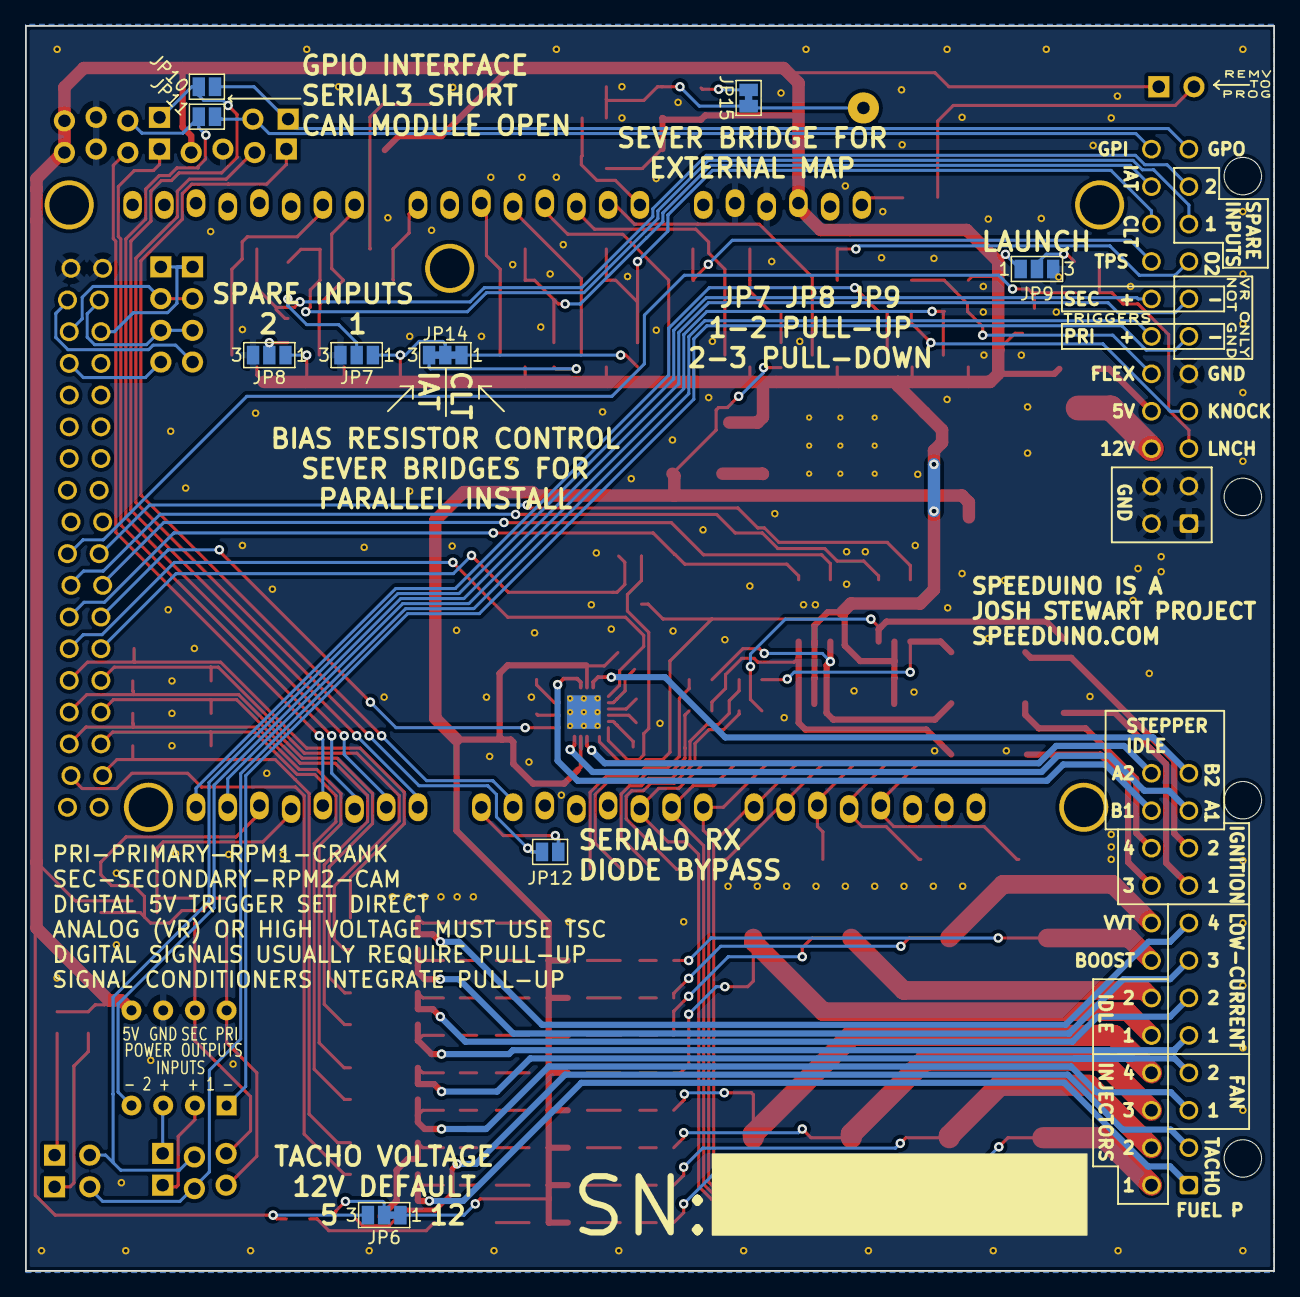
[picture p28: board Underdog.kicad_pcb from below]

Board: 2 copper layers, 100.0 x 99.8 mm, 213 parts (10 on the bottom side), 162 nets.

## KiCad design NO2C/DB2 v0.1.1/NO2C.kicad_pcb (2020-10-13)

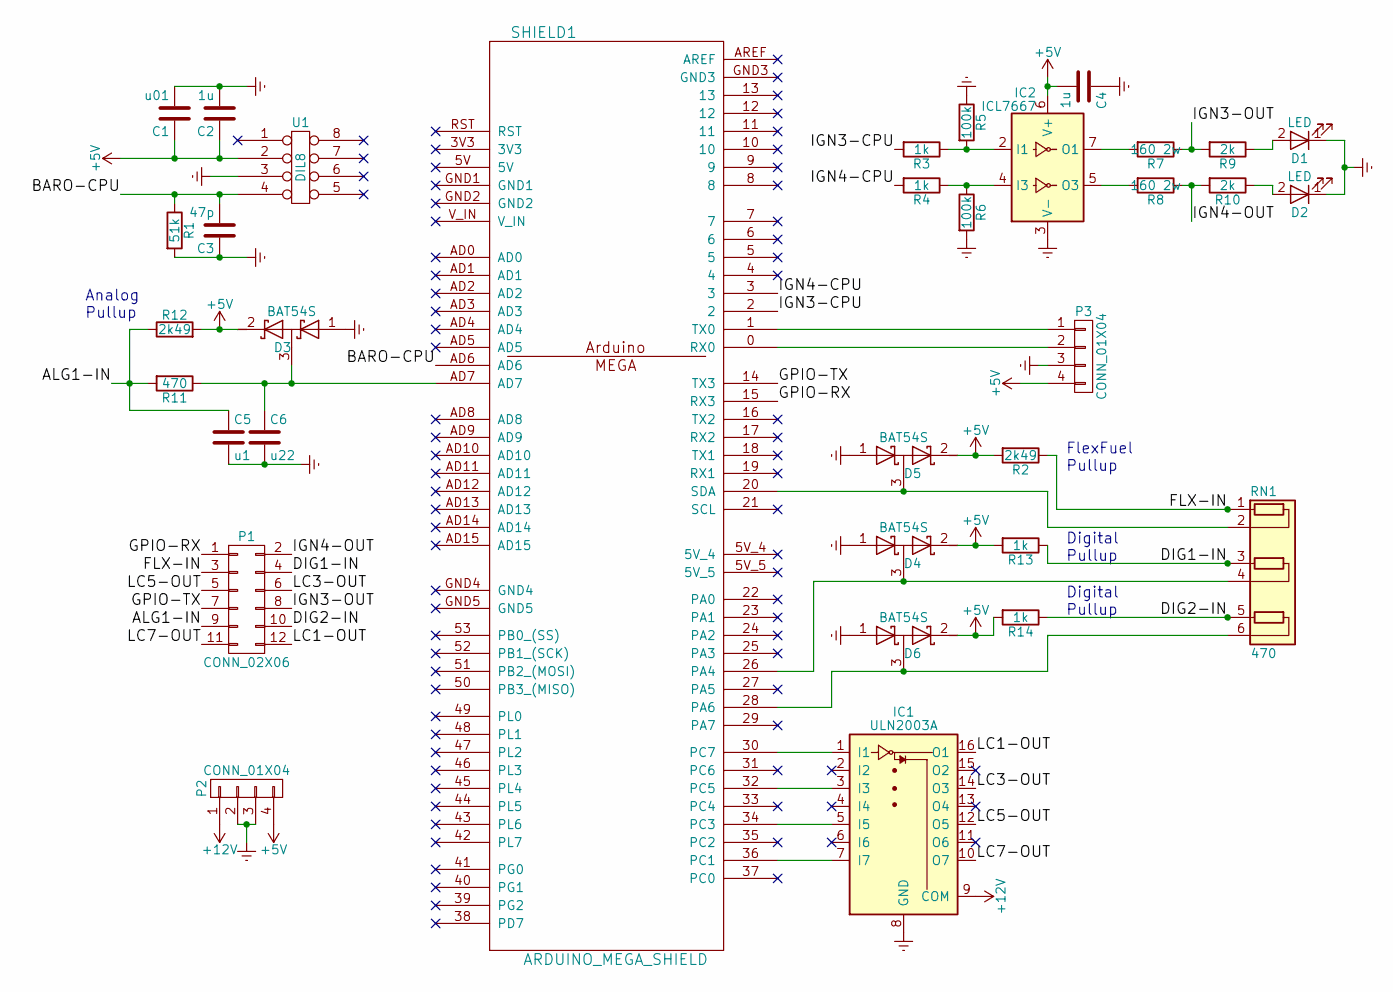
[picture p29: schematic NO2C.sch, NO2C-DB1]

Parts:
C1: u01; C_Disc_D3.8mm_W2.6mm_P2.50mm
C2, C4: 1u; C_Disc_D5.1mm_W3.2mm_P5.00mm
C3: 47p; C_1206_HandSoldering
C5: u1; C_Disc_D3.8mm_W2.6mm_P2.50mm
C6: u22; C_Disc_D3.8mm_W2.6mm_P2.50mm
D1, D2: LED; LED_D3.0mm
D3, D4, D5, D6: BAT54S; SOT-23_Handsoldering
IC1: ULN2003A; SOIC-16_3.9x9.9mm_Pitch1.27mm
IC2: ICL7667; DIP-8_W7.62mm
P1: CONN_02X06; Molex_Microfit3_Header_02x06_Straight_43045-1228
P2, P3: CONN_01X04; Pin_Header_Straight_1x04_Pitch2.54mm
R1: 51k; R_1206_HandSoldering
R2, R12: 2k49; R_Axial_DIN0207_L6.3mm_D2.5mm_P7.62mm_Horizontal
R3, R4: 1k; R_Axial_DIN0207_L6.3mm_D2.5mm_P7.62mm_Horizontal
R5, R6: 100k; R_Axial_DIN0204_L3.6mm_D1.6mm_P7.62mm_Horizontal
R7, R8: 160 2w; R_Axial_DIN0411_L9.9mm_D3.6mm_P12.70mm_Horizontal
R9, R10: 2k; R_Axial_DIN0207_L6.3mm_D2.5mm_P7.62mm_Horizontal
R11: 470; R_Axial_DIN0207_L6.3mm_D2.5mm_P7.62mm_Horizontal
R13, R14: 1k; R_1206
RN1: 470; R_Array_SIP6
SHIELD1: ARDUINO_MEGA_SHIELD; ARDUINO_MEGA_SHIELD_DB
U1: DIL8; SSO-8_9.6x6.3mm_Pitch1.27mm_Clearance10.5mm

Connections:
+5V: C1.1, C2.1, C4.2, D3.2 (K), D4.2 (K), D5.2 (K), D6.2 (K), IC2.6 (V+), P2.4, P3.4, R2.2, R12.2, R13.2, R14.2, U1.2
+12V: IC1.9 (COM), P2.1
/ALG1-IN: C5.1, P1.9, R11.2, R12.1
/BARO-CPU: C3.2, R1.1, SHIELD1.AD6, U1.4
/DIG1-IN: P1.4, R13.1, RN1.3 (R2.1)
/DIG2-IN: P1.10, R14.1, RN1.5 (R3.1)
/FLX-IN: P1.3, R2.1, RN1.1 (R1.1)
/GPIO-RX: P1.1, SHIELD1.15 (RX3)
/GPIO-TX: P1.7, SHIELD1.14 (TX3)
/IGN3-CPU: R3.2, SHIELD1.2
/IGN3-OUT: P1.8, R7.1, R9.2
/IGN4-CPU: R4.2, SHIELD1.3
/IGN4-OUT: P1.2, R8.1, R10.2
/LC1-OUT: IC1.16 (O1), P1.12
/LC3-OUT: IC1.14 (O3), P1.6
/LC5-OUT: IC1.12 (O5), P1.5
/LC7-OUT: IC1.10 (O7), P1.11
Earth: C1.2, C2.2, C3.1, C4.1, C5.2, C6.2, D1.1 (K), D2.1 (K), D3.1 (A), D4.1 (A), D5.1 (A), D6.1 (A), IC1.8 (GND), IC2.3 (V-), P2.2, P2.3, P3.3, R1.2, R5.1, R6.2, U1.3
unnamed: C6.1, D3.3 (common), R11.1, SHIELD1.AD7
unnamed: D1.2 (A), R9.1
unnamed: D2.2 (A), R10.1
unnamed: D4.3 (common), RN1.4 (R2.2), SHIELD1.26 (PA4)
unnamed: D5.3 (common), RN1.2 (R1.2), SHIELD1.20 (SDA)
unnamed: D6.3 (common), RN1.6 (R3.2), SHIELD1.28 (PA6)
unnamed: IC1.1 (I1), SHIELD1.30 (PC7)
unnamed: IC1.3 (I3), SHIELD1.32 (PC5)
unnamed: IC1.5 (I5), SHIELD1.34 (PC3)
unnamed: IC1.7 (I7), SHIELD1.36 (PC1)
unnamed: IC2.2 (I1), R3.1, R5.2
unnamed: IC2.4 (I3), R4.1, R6.1
unnamed: IC2.5 (O3), R8.2
unnamed: IC2.7 (O1), R7.2
unnamed: P3.1, SHIELD1.1 (TX0)
unnamed: P3.2, SHIELD1.0 (RX0)

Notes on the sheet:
FlexFuel Pullup
Digital Pullup
Analog Pullup

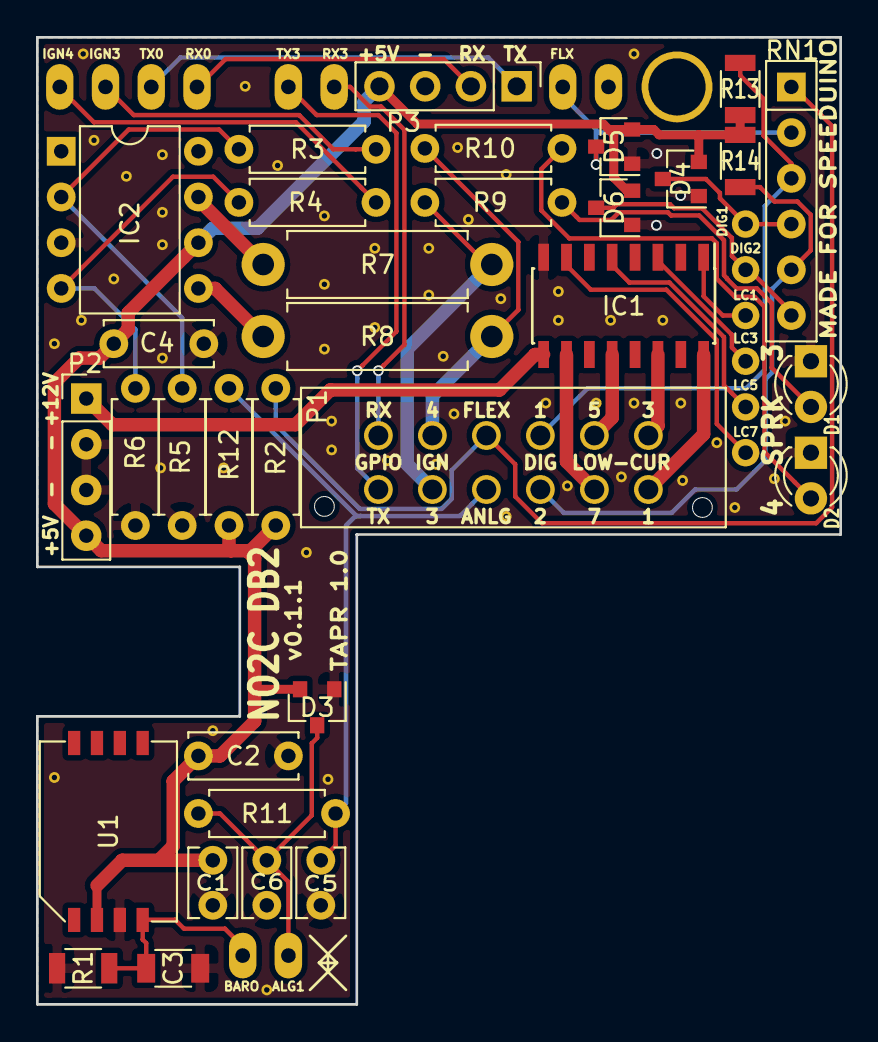
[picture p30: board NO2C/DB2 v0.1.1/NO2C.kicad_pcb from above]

Board: 2 copper layers, 44.6 x 53.7 mm, 34 parts (0 on the bottom side), 34 nets.

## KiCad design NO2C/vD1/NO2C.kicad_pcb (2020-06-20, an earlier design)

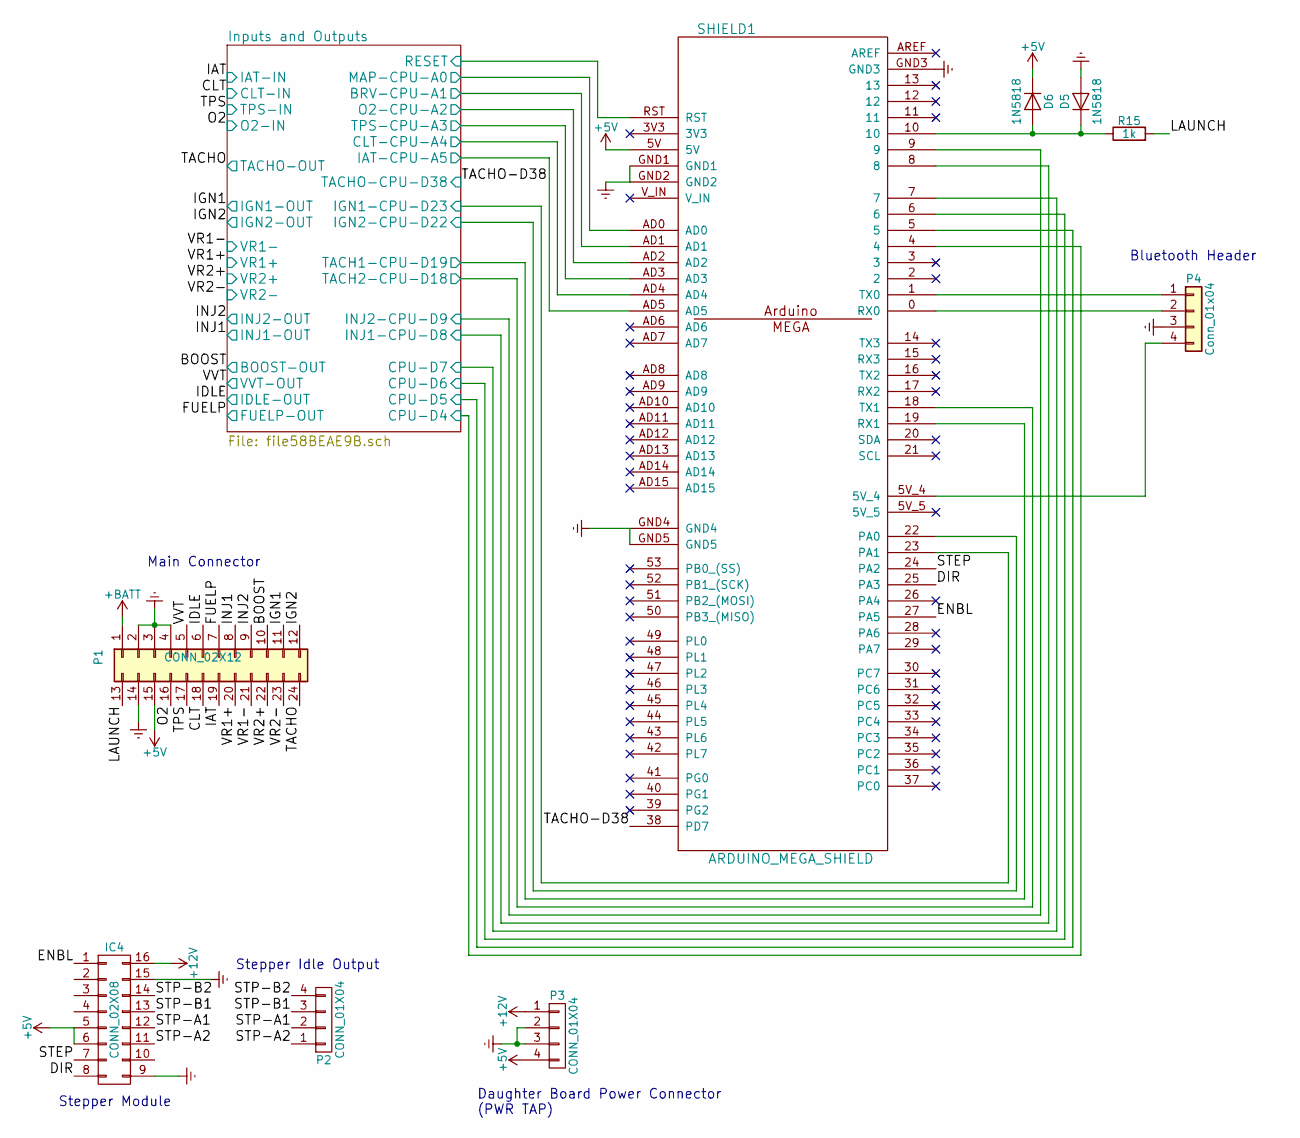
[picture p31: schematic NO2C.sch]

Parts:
D5, D6: 1N5818; D_DO-41_SOD81_P7.62mm_Horizontal
IC4: CONN_02X08; DRV8825
P1: CONN_02X12; Molex_Microfit3_Header_02x12_Straight_43045-2428
P2: CONN_01X04; Molex_Microfit3_Header_02x02_Angled_43045-040x
P3: CONN_01X04; Pin_Header_Straight_1x04_Pitch2.54mm
P4: Conn_01x04; Socket_Strip_Straight_1x04_Pitch2.54mm
R15: 1k; R_Axial_DIN0207_L6.3mm_D2.5mm_P7.62mm_Horizontal
SHIELD1: ARDUINO_MEGA_SHIELD

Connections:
+5V: D6.1 (K), IC4.5, IC4.6, P1.15, P3.4, SHIELD1.5V; also elsewhere on the board
+12V: IC4.16, P1.1, P3.1; also elsewhere on the board
/BOOST: P1.10; also elsewhere on the board
/CLT: P1.18; also elsewhere on the board
/DIR: IC4.8, SHIELD1.25 (PA3)
/ENBL: IC4.1, SHIELD1.27 (PA5)
/FUELP: P1.7; also elsewhere on the board
/IAT: P1.19; also elsewhere on the board
/IDLE: P1.6; also elsewhere on the board
/IGN1: P1.11; also elsewhere on the board
/IGN2: P1.12; also elsewhere on the board
/INJ1: P1.8; also elsewhere on the board
/INJ2: P1.9; also elsewhere on the board
/Inputs and Outputs/BRV-CPU-A1: SHIELD1.AD1; also elsewhere on the board
/Inputs and Outputs/CLT-CPU-A4: SHIELD1.AD4; also elsewhere on the board
/Inputs and Outputs/CPU-D4: SHIELD1.4; also elsewhere on the board
/Inputs and Outputs/CPU-D5: SHIELD1.5; also elsewhere on the board
/Inputs and Outputs/CPU-D6: SHIELD1.6; also elsewhere on the board
/Inputs and Outputs/CPU-D7: SHIELD1.7; also elsewhere on the board
/Inputs and Outputs/IAT-CPU-A5: SHIELD1.AD5; also elsewhere on the board
/Inputs and Outputs/IGN1-CPU-D23: SHIELD1.23 (PA1); also elsewhere on the board
/Inputs and Outputs/IGN2-CPU-D22: SHIELD1.22 (PA0); also elsewhere on the board
/Inputs and Outputs/INJ1-CPU-D8: SHIELD1.8; also elsewhere on the board
/Inputs and Outputs/INJ2-CPU-D9: SHIELD1.9; also elsewhere on the board
/Inputs and Outputs/MAP-CPU-A0: SHIELD1.AD0; also elsewhere on the board
/Inputs and Outputs/O2-CPU-A2: SHIELD1.AD2; also elsewhere on the board
/Inputs and Outputs/RESET: SHIELD1.RST; also elsewhere on the board
/Inputs and Outputs/TACH1-CPU-D19: SHIELD1.19 (RX1); also elsewhere on the board
/Inputs and Outputs/TACH2-CPU-D18: SHIELD1.18 (TX1); also elsewhere on the board
/Inputs and Outputs/TPS-CPU-A3: SHIELD1.AD3; also elsewhere on the board
/LAUNCH: P1.13, R15.2
/O2: P1.16; also elsewhere on the board
/STEP: IC4.7, SHIELD1.24 (PA2)
/STP-A1: IC4.12, P2.2
/STP-A2: IC4.11, P2.1
/STP-B1: IC4.13, P2.3
/STP-B2: IC4.14, P2.4
/TACHO: P1.24; also elsewhere on the board
/TACHO-D38: SHIELD1.38 (PD7); also elsewhere on the board
/TPS: P1.17; also elsewhere on the board
/VR1+: P1.20; also elsewhere on the board
/VR1-: P1.21; also elsewhere on the board
/VR2+: P1.22; also elsewhere on the board
/VR2-: P1.23; also elsewhere on the board
/VVT: P1.5; also elsewhere on the board
Earth: D5.2 (A), IC4.9, IC4.15, P1.2, P1.3, P1.4, P1.14, P3.2, P3.3, P4.3, SHIELD1.GND1, SHIELD1.GND2, SHIELD1.GND3, SHIELD1.GND4, SHIELD1.GND5; also elsewhere on the board
unnamed: D5.1 (K), D6.2 (A), R15.1, SHIELD1.10
unnamed: P4.1, SHIELD1.1 (TX0)
unnamed: P4.2, SHIELD1.0 (RX0)
unnamed: P4.4, SHIELD1.5V_4

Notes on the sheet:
Stepper Module
Daughter Board Power Connector (PWR TAP)
Bluetooth Header
Stepper Idle Output
Main Connector

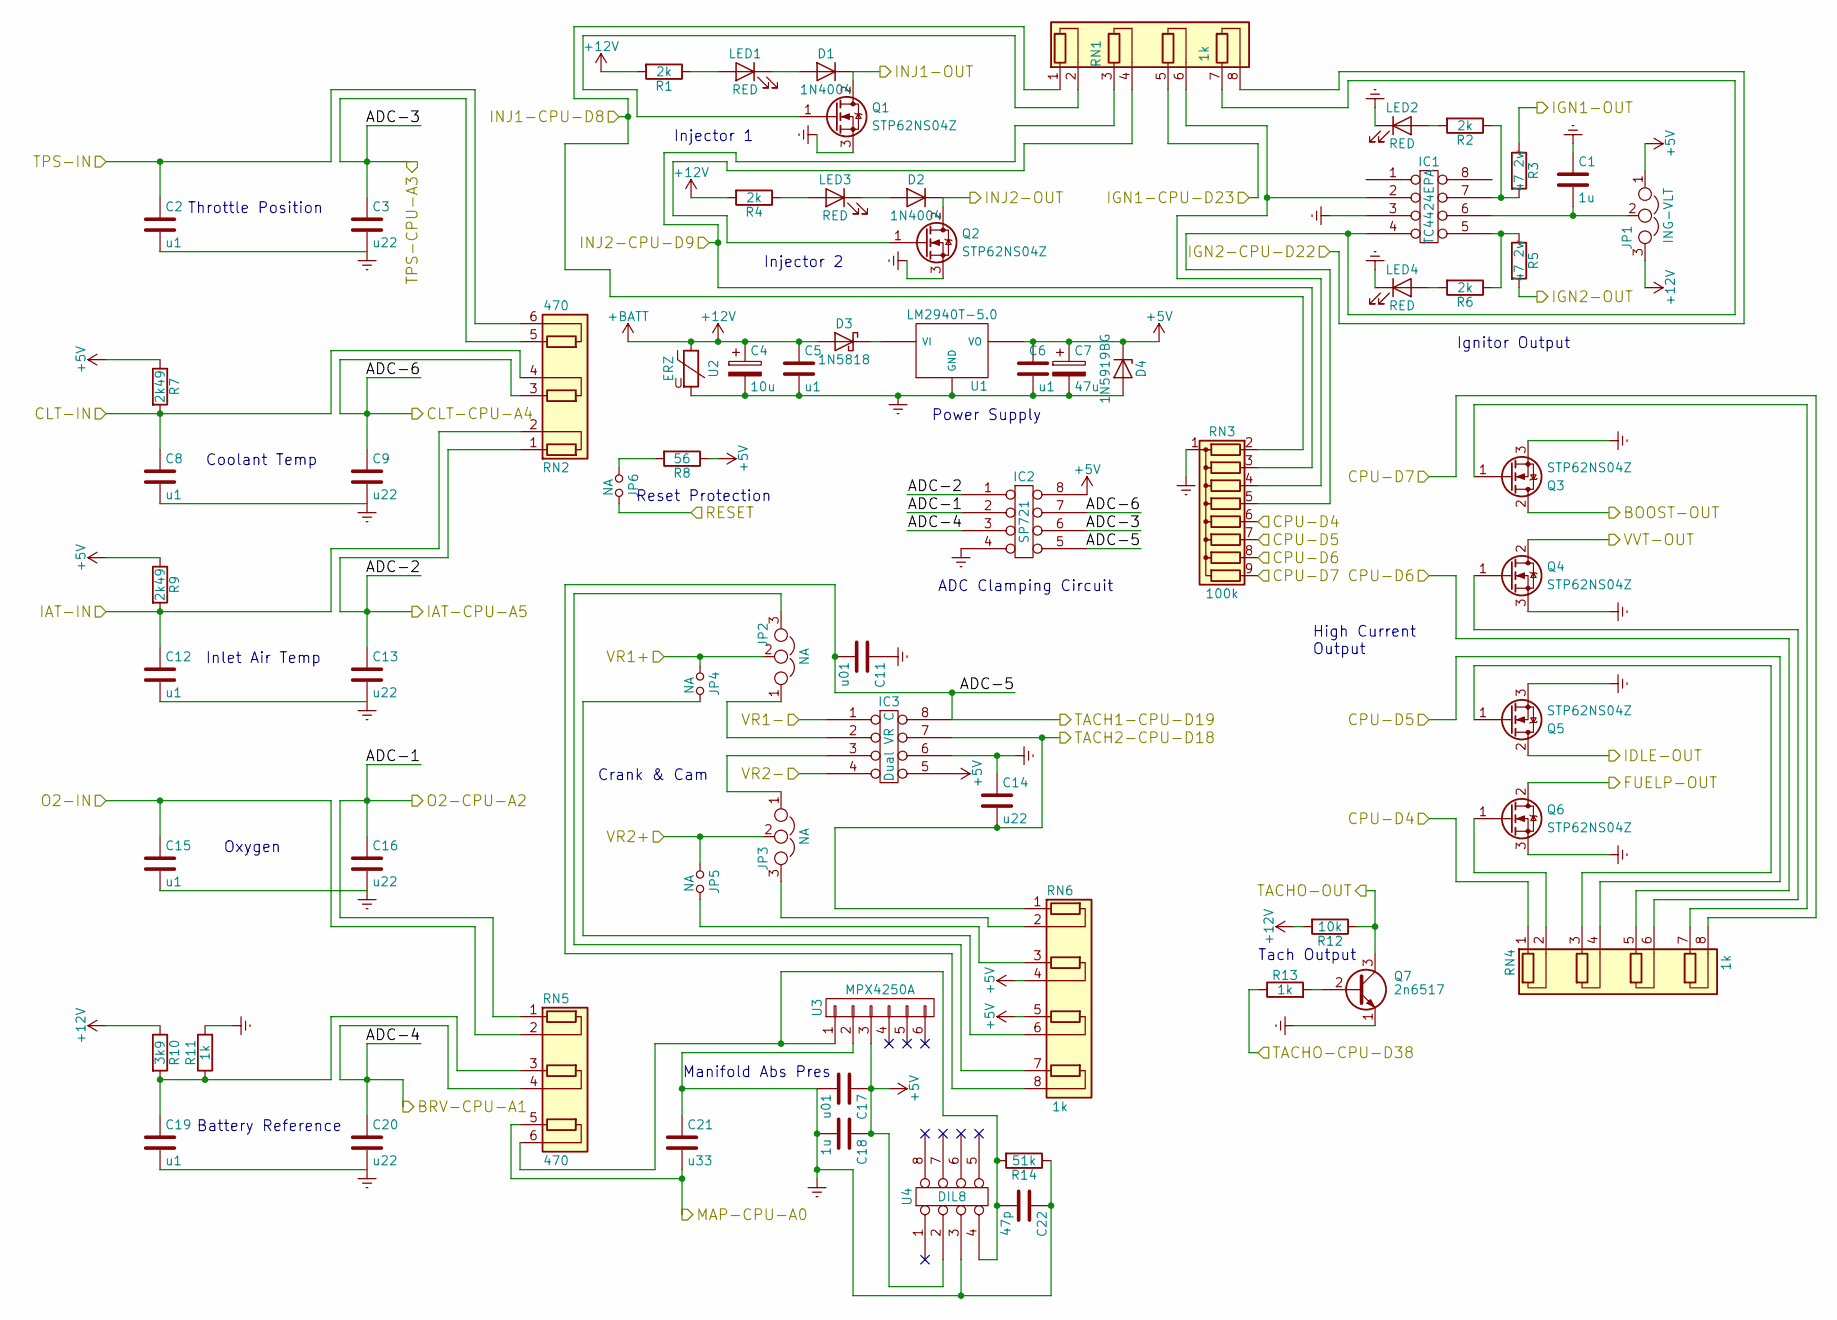
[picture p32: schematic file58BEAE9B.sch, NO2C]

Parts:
C1, C18: 1u; C_Disc_D6.0mm_W2.5mm_P5.00mm
C2, C5, C6, C8, C12, C15, C19: u1; C_Disc_D3.8mm_W2.6mm_P2.50mm
C3, C9, C13, C14, C16, C20: u22; C_Disc_D3.8mm_W2.6mm_P2.50mm
C4: 10u; CP_Radial_Tantal_D6.0mm_P2.50mm
C7: 47u; CP_Radial_Tantal_D6.0mm_P2.50mm
C11, C17: u01; C_Disc_D3.8mm_W2.6mm_P2.50mm
C21: u33; C_Disc_D3.8mm_W2.6mm_P2.50mm
C22: 47p; C_1206
D1, D2: 1N4004; D_DO-41_SOD81_P7.62mm_Horizontal
D3: 1N5818; D_DO-41_SOD81_P7.62mm_Horizontal
D4: 1N5919BG; D_DO-41_SOD81_P7.62mm_Horizontal
IC1: TC4424EPA; DIP-8_W7.62mm
IC2: SP721; DIP-8_W7.62mm
IC3: Dual VR C; DIP-8_W7.62mm_Socket
JP1: ING-VLT; Pin_Header_Straight_1x03_Pitch2.54mm
JP2, JP3: NA; Pin_Header_Straight_1x03_Pitch2.54mm
JP4, JP5, JP6: NA; Pin_Header_Straight_1x02_Pitch2.54mm
LED1, LED2, LED3, LED4: RED; LED_D3.0mm
Q1, Q2, Q3, Q4, Q5, Q6: STP62NS04Z; TO-220_Vertical
Q7: 2n6517; TO-92_Molded_Narrow
R1, R2, R4, R6: 2k; R_Axial_DIN0207_L6.3mm_D2.5mm_P7.62mm_Horizontal
R3, R5: 47 2w; R_Axial_DIN0411_L9.9mm_D3.6mm_P12.70mm_Horizontal
R7, R9: 2k49; R_Axial_DIN0207_L6.3mm_D2.5mm_P7.62mm_Horizontal
R8: 56; R_Axial_DIN0207_L6.3mm_D2.5mm_P7.62mm_Horizontal
R10: 3k9; R_Axial_DIN0207_L6.3mm_D2.5mm_P7.62mm_Horizontal
R11, R13: 1k; R_Axial_DIN0207_L6.3mm_D2.5mm_P7.62mm_Horizontal
R12: 10k; R_Axial_DIN0207_L6.3mm_D2.5mm_P7.62mm_Horizontal
R14: 51k; R_1206
RN1, RN4, RN6: 1k; R_Array_SIP8
RN2, RN5: 470; R_Array_SIP6
RN3: 100k; R_Array_SIP9
U1: LM2940T-5.0; TO-220_Vertical
U2: ERZ; RV_Disc_D15.5_W4.2_P7.5
U3: MPX4250A
U4: DIL8; NXP_Pressure_Sensor_SSOP

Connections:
+5V: C6.1, C7.1, C17.1, C18.1, D4.1 (K), IC2.8, IC3.5, JP1.1, R7.1, R8.1, R9.1, RN6.4 (R2.2), RN6.5 (R3.1), U1.3 (VO), U3.3, U4.2; also elsewhere on the board
+12V: C4.1, C5.1, D3.2 (A), JP1.3, R1.2, R4.2, R10.1, R12.2, U2.1; also elsewhere on the board
/BOOST: Q3.2 (D); also elsewhere on the board
/CLT: C8.1, R7.2, RN2.4 (R2.2); also elsewhere on the board
/FUELP: Q6.2 (D); also elsewhere on the board
/IAT: C12.1, R9.2, RN2.2 (R1.2); also elsewhere on the board
/IDLE: Q5.2 (D); also elsewhere on the board
/IGN1: R3.1; also elsewhere on the board
/IGN2: R5.2; also elsewhere on the board
/INJ1: D1.1 (K), Q1.2 (D); also elsewhere on the board
/INJ2: D2.1 (K), Q2.2 (D); also elsewhere on the board
/Inputs and Outputs/BRV-CPU-A1: C20.1, IC2.3, RN5.4 (R2.2); also elsewhere on the board
/Inputs and Outputs/CLT-CPU-A4: C9.1, IC2.7, RN2.3 (R2.1); also elsewhere on the board
/Inputs and Outputs/CPU-D4: RN3.6 (R5), RN4.1 (R1.1); also elsewhere on the board
/Inputs and Outputs/CPU-D5: RN3.7 (R6), RN4.4 (R2.2); also elsewhere on the board
/Inputs and Outputs/CPU-D6: RN3.8 (R7), RN4.5 (R3.1); also elsewhere on the board
/Inputs and Outputs/CPU-D7: RN3.9 (R8), RN4.8 (R4.2); also elsewhere on the board
/Inputs and Outputs/IAT-CPU-A5: C13.1, IC2.1, RN2.1 (R1.1); also elsewhere on the board
/Inputs and Outputs/IGN1-CPU-D23: RN1.5 (R3.1); also elsewhere on the board
/Inputs and Outputs/IGN2-CPU-D22: RN1.8 (R4.2); also elsewhere on the board
/Inputs and Outputs/INJ1-CPU-D8: RN1.1 (R1.1), RN3.2 (R1); also elsewhere on the board
/Inputs and Outputs/INJ2-CPU-D9: RN1.3 (R2.1), RN3.3 (R2); also elsewhere on the board
/Inputs and Outputs/MAP-CPU-A0: C21.2, RN5.5 (R3.1); also elsewhere on the board
/Inputs and Outputs/O2-CPU-A2: C16.1, IC2.2, RN5.1 (R1.1); also elsewhere on the board
/Inputs and Outputs/RESET: JP6.2; also elsewhere on the board
/Inputs and Outputs/TACH1-CPU-D19: C11.2, IC2.5, IC3.8, RN6.8 (R4.2); also elsewhere on the board
/Inputs and Outputs/TACH2-CPU-D18: C14.2, IC3.7, RN6.1 (R1.1); also elsewhere on the board
/Inputs and Outputs/TPS-CPU-A3: C3.1, IC2.6, RN2.5 (R3.1); also elsewhere on the board
/O2: C15.1, RN5.2 (R1.2); also elsewhere on the board
/TACHO: Q7.3 (C), R12.1; also elsewhere on the board
/TACHO-D38: R13.1; also elsewhere on the board
/TPS: C2.1, RN2.6 (R3.2); also elsewhere on the board
/VR1+: JP2.2, JP4.1; also elsewhere on the board
/VR1-: IC3.1; also elsewhere on the board
/VR2+: JP3.2, JP5.1; also elsewhere on the board
/VR2-: IC3.4; also elsewhere on the board
/VVT: Q4.2 (D); also elsewhere on the board
Earth: C1.1, C2.2, C3.2, C4.2, C5.2, C6.2, C7.2, C8.2, C9.2, C11.1, C12.2, C13.2, C14.1, C15.2, C16.2, C17.2, C18.2, C19.2, C20.2, C21.1, C22.1, D4.2 (A), IC1.3, IC2.4, IC3.6, LED2.1 (K), LED4.1 (K), Q1.3 (S), Q2.3 (S), Q3.3 (S), Q4.3 (S), Q5.3 (S), Q6.3 (S), Q7.1 (E), R11.2, R14.1, RN3.1 (common), U1.2 (GND), U2.2, U3.2, U4.3; also elsewhere on the board
unnamed: C1.2, IC1.6, JP1.2
unnamed: C19.1, R10.2, R11.1, RN5.3 (R2.1)
unnamed: C22.2, R14.2, RN5.6 (R3.2), U3.1, U4.4
unnamed: D1.2 (A), LED1.1 (K)
unnamed: D2.2 (A), LED3.1 (K)
unnamed: D3.1 (K), U1.1 (VI)
unnamed: IC1.2, RN1.6 (R3.2), RN3.4 (R3)
unnamed: IC1.4, RN1.7 (R4.1), RN3.5 (R4)
unnamed: IC1.5, R5.1, R6.1
unnamed: IC1.7, R2.1, R3.2
unnamed: IC3.2, JP2.1
unnamed: IC3.3, JP3.1
unnamed: JP2.3, RN6.7 (R4.1)
unnamed: JP3.3, RN6.2 (R1.2)
unnamed: JP4.2, RN6.6 (R3.2)
unnamed: JP5.2, RN6.3 (R2.1)
unnamed: JP6.1, R8.2
unnamed: LED1.2 (A), R1.1
unnamed: LED2.2 (A), R2.2
unnamed: LED3.2 (A), R4.1
unnamed: LED4.2 (A), R6.2
unnamed: Q1.1 (G), RN1.2 (R1.2)
unnamed: Q2.1 (G), RN1.4 (R2.2)
unnamed: Q3.1 (G), RN4.7 (R4.1)
unnamed: Q4.1 (G), RN4.6 (R3.2)
unnamed: Q5.1 (G), RN4.3 (R2.1)
unnamed: Q6.1 (G), RN4.2 (R1.2)
unnamed: Q7.2 (B), R13.2

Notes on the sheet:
Throttle Position
Inlet Air Temp
Coolant Temp
Oxygen
Battery Reference
Manifold Abs Pres
Crank & Cam
ADC Clamping Circuit
Reset Protection
Power Supply
Injector 1
Injector 2
Ignitor Output
Tach Output
High Current Output


Board: 2 copper layers, 99.4 x 53.7 mm, 78 parts (0 on the bottom side), 78 nets.

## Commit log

2017-10-20 Add files via upload
    Added NO2C v0.2.0 files
    [NO2C-v0.2.0-BOM.ods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]
2017-10-20 Add files via upload
    Added NO2C v0.1.1 files
    [NO2C-W-STEPPER-BOM.ods, NO2C-W-STEPPER-BOM.xls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]
2017-11-04 BOM and Code Changes
    Removed CODE folder as the latest version is now in main Speeduino project. Updated v0.1.1 BOM.
    [NO2C-W-STEPPER-BOM.ods, NO2C-W-STEPPER-BOM.xls]
2017-11-18 Updated BOM
    Added more connector information.
    [NO2C-v0.2.0-BOM.ods]
2017-11-18 BOM Changes
    Add high voltage tacho transistor option.
    [NO2C-v0.2.0-BOM.ods]
2017-11-22 More BOM info
    [NO2C-v0.2.0-BOM.ods]
2017-12-31 BOM Tweeks Schema Add
    [NO2C-v0.2.0-BOM.ods]
2018-01-23 Corrected jumper numbers in BOM
    [NO2C-v0.2.0-BOM.ods]
2018-02-02 Update BOM, Arrange folders for future versions
    [NO2C-B.Cu.gbl, NO2C-B.Mask.gbs, NO2C-B.SilkS.gbo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]
2018-03-18 Upload of NO2C v0.2.1
    [NO2C-v0.2.0-BOM.ods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]
2018-06-03 NO2C v.0.2.2
    [NO2C-v0.2.x-BOM.ods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]
2018-08-05 Added NO2C Case STL
    [Set-NOboxT.stl]
2018-12-17 Added UA4C vA3 Schematics
2018-12-17 Added UA4C vA3 Design Files
    [INS.sch, OUTS.sch, POWER.sch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]
2019-08-24 New UA4C and NO2C revisions
    Added new board revisions and organized files
    [INS.sch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]
2019-08-27 Correct UA4C vB1 files
    Layout, schematics and renders were from old version
2019-11-17 Add Connector Application Guide
    Added Minitek PWR 3.0 Application information with details about how the 3mm connections are assembled, both standard and high-current.
2020-06-20 Added UA4CvB2 and NO2CvD1 information
    [INS.sch, NO2C-2018-08-18-14-43-34.sch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]
2020-10-13 Add DB2
    [NO2C-v0.2.x-DB2-BOM.ods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]
2022-03-21 Add new UA4C revisions
    B3, C2, C3
    [INS.sch, OUTS.sch, POWER.sch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]
2022-03-21 Updated board layout files
    [Underdog.kicad_pcb]
2024-01-24 UA4C C4 C5
    New revision upload
    [INS.kicad_sch, OUTS.kicad_sch, POWER.kicad_sch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]
2024-06-26 Create Ocelot Connector Mapping.pdf
2024-09-20 Updated connector map file
    Fixed pin connector pin number and added some color
2024-10-25 Updated Ocelot connector sheet
    Slightly changed colors to match future pigtails and added some quick tips.
